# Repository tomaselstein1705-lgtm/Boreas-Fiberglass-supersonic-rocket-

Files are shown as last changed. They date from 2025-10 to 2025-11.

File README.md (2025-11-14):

# Boreas
Boreas is a full fiberglass 90cm long rocket, expected to reach up to 2km and fly over Mach 1 (Mach 1.2 actually), in an I205W high power motor, utilizing dual development and other high-power rocketry techniques. If you want to make it yourself, I recommend you first get your L1 with another rocket; handling fiberglass is very dangerous and difficult, so do it at your own risk!! Also, this rocket doesn't have any railguides, so you'll need to build a 40mm launch tower or just go to a club and use the one they have. Be really careful handling motors and always follow NAR/TRIPOLI rules!!!

# Boreas render
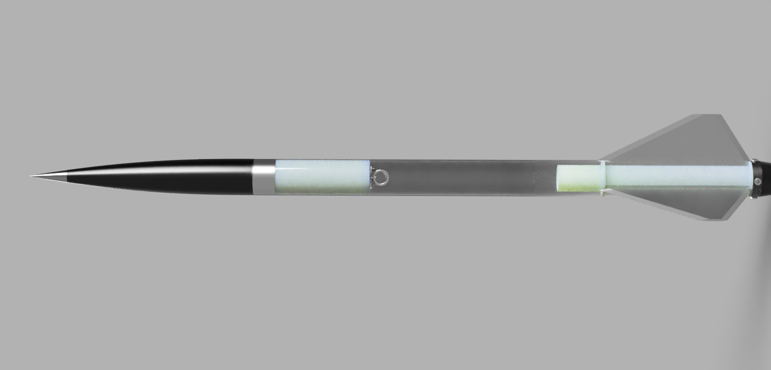
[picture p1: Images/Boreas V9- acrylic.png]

Full body (low visibility)

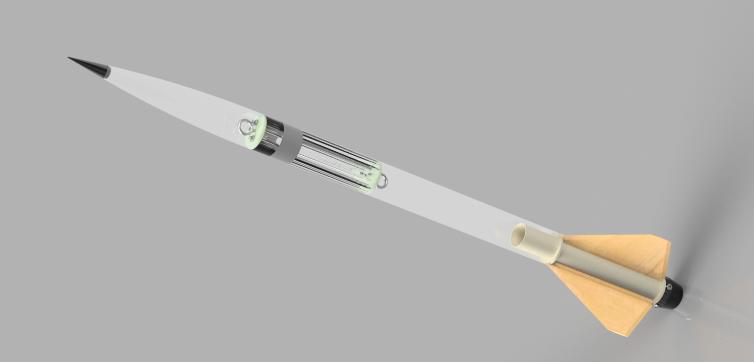
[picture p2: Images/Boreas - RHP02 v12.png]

Full body (Invisible body)

# BOM
(Without a motor, you can use an "I-205" or smaller, make simulations before flying)

| Name | Description | Quantity | Final Price | Link |
|---|---|---|---|---|
| Shock Cord - 1500 lb | Good quality, they are made for high power, and kevlar is the material of choice for shock cords | 4 m | $6.5 | https://www.mach1rocketry.com/product-page/kevlar-shock-cords |
| Centering rings | Made out of G10, they are precise and get the job done | 2 | $8 | https://www.mach1rocketry.com/product-page/g10-fiberglass-centering-rings |
| 29mm MMT | Good fiberglass mount | 9 in | $11.25 | https://www.mach1rocketry.com/product-page/fiberglass-motor-mount-tubes |
| Light fiberglass sleeve | Used to fabricate the nosecone; remnants are cheaper and work just as well | 15 ft | $7.95 | https://sollercompositesllc.com/product/remnants/ |
| 40mm Airframe | Premade, light, and inexpensive fiberglass airframe tube | 3 ft | $39 | https://www.mach1rocketry.com/product-page/fiberglass-airframe-tubes |
| Shock Cord - 1500 lb | Same kevlar shock cord as above | 4 m | $6.5 | https://www.mach1rocketry.com/product-page/fiberglass-coupler-tubes |
| 38mm avbay tube | The avionics fit inside this tube | 5 in | $8.75 | https://www.mach1rocketry.com/product-page/fiberglass-coupler-tubes |
| .9 grams charge wells | Holds the ejection charge; lightweight with a 3M screw on the bottom | 2 | $8 | https://www.mach1rocketry.com/product-page/charge-wells |
| Eggtimer Quark (backup) | Backup commercial flight computer for safety | 1 | $25 | https://eggtimerrocketry.com/purchase/ |
| HighTel (main flight computer) | Custom flight computer | 1 | None | https://github.com/tomaselstein1705-lgtm/HighTel |
| Terminal blocks | Connection point for pyro igniters; computers send charge through these | 1 | $2.5 | https://www.mach1rocketry.com/product-page/terminal-blocks |
| M4 Eye nuts | Cheap eye nuts including bolts and washers | 3 | $6 | https://www.mach1rocketry.com/product-page/eye-nuts |
| Thin mill drogue chute (9\") | Drogue locks in terminal velocity until main deployment; very durable brand | 1 | $6 | https://www.mach1rocketry.com/product-page/top-flight-thin-mill-parachutes |
| Thin mill parachute (24\") | Main chute brings descent to 6 m/s; durable and reliable | 1 | $19 | https://www.mach1rocketry.com/product-page/top-flight-thin-mill-parachutes |
| Table top epoxy (2 quart) | Used for tip-to-tip reinforcement and nosecone fabrication; cheap and effective | 1 | $34 | https://www.totalboat.com/products/table-top-epoxy-crystal-clear-resin |
| Aeropoxy ES6209 | Thick, strong, and affordable epoxy for fiberglass | 1 | $40 | https://giantleaprocketry.com/products/aeropoxy-structural-adhesive-kit |
| 3K Carbon Twill Weave | Carbon fiber cloth upgrade, sold by the yard | 1 yd | $19.99 | https://sollercompositesllc.com/product/3k-carbon-twill-weave-sold-by-the-running-yard-roll/ |

| **Total Cost:**                          |                                                                                                                                                                                        |          | **241.94$** |      |

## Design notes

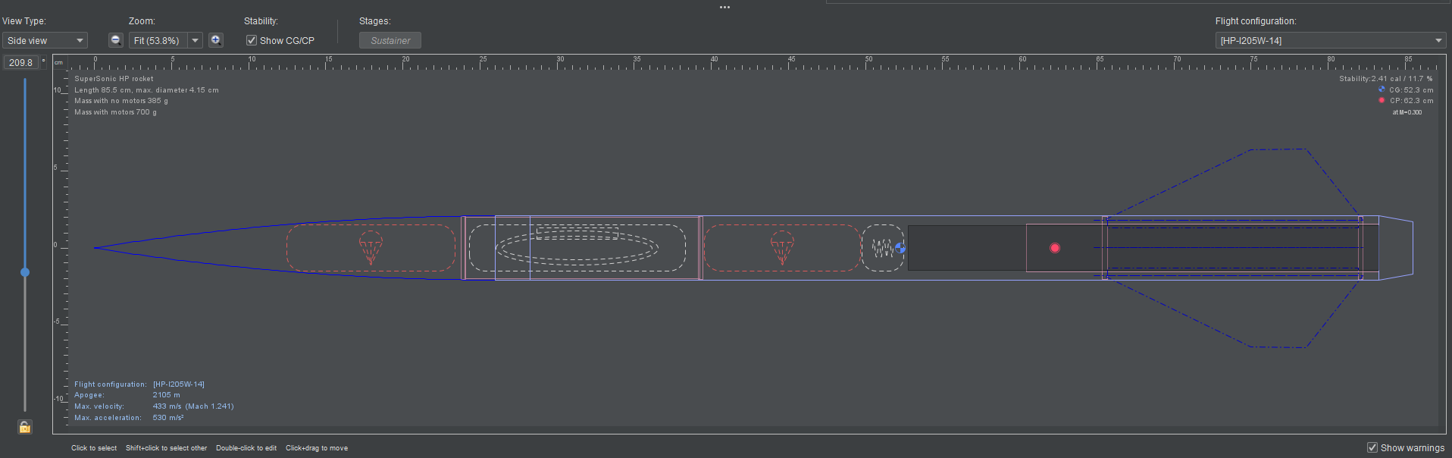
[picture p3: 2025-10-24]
Images/OrOverview.png

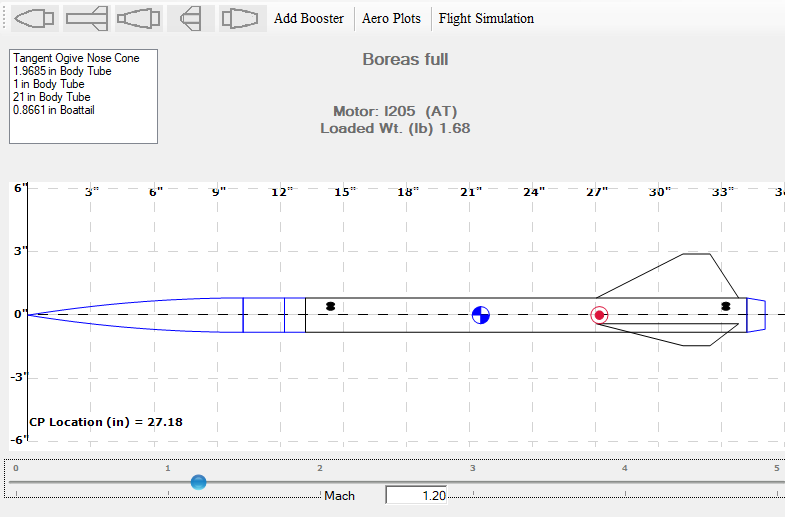
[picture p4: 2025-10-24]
Images/RASAoverview.png

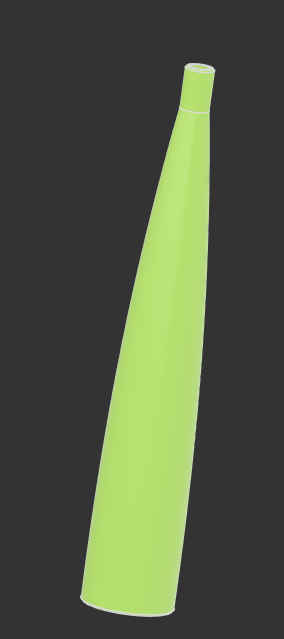
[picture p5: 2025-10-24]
Images/Noseconemodl.png

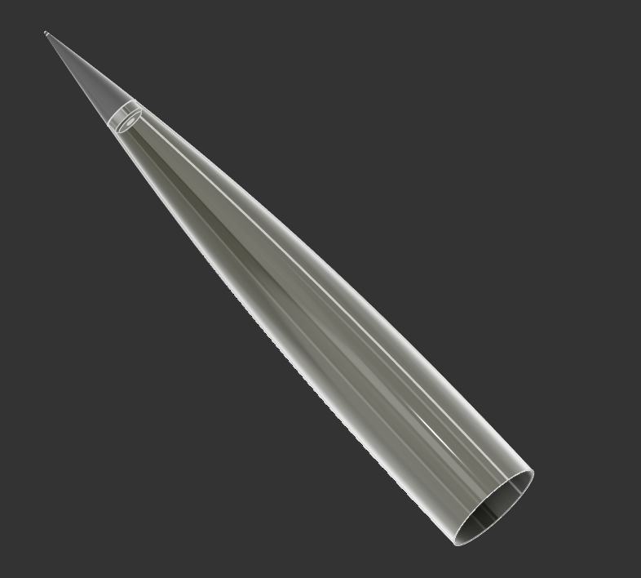
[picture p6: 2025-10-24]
Images/NoseCone.png

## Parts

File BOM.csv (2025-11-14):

Name | Description | Quantity | Final Price | Link
Shock Cord - 1500 lb | Good quality Kevlar cords for high power rockets | 4 m | $6.50 | https://www.mach1rocketry.com/product-page/kevlar-shock-cords
Centering Rings | Made of G10 fiberglass; precise and durable | 2 | $8.00 | https://www.mach1rocketry.com/product-page/g10-fiberglass-centering-rings
29mm MMT | Fiberglass motor mount tube | 9 in | $11.25 | https://www.mach1rocketry.com/product-page/fiberglass-motor-mount-tubes
I205 14A 29mm Motor | High-performance motor — the heart of the rocket | 1 | $64.00 | https://aerotech-rocketry.com/products/product_6195f3f3-6684-3bea-d54d-0b09b58c0427
Light Fiberglass Sleeve | Used for fabricating the nosecone; remnants are cost-effective | 15 ft | $7.95 | https://sollercompositesllc.com/product/remnants/
40mm Airframe | Premade fiberglass tube for rocket airframe — lightweight and affordable | 3 ft | $39.00 | https://www.mach1rocketry.com/product-page/fiberglass-airframe-tubes
38mm AvBay Tube | Houses avionics section of the rocket | 5 in | $8.75 | https://www.mach1rocketry.com/product-page/fiberglass-coupler-tubes
0.9g Charge Wells | Holds ejection charges; light and includes screw base | 2 | $8.00 | https://www.mach1rocketry.com/product-page/charge-wells
Eggtimer Quark (Backup) | Backup commercial flight computer for redundancy and safety | 1 | $25.00 | https://eggtimerrocketry.com/purchase/
HighTel (Main Flight Computer) | Custom flight computer — see GitHub repository | 1 | N/A | https://github.com/tomaselstein1705-lgtm/HighTel
Terminal Blocks | Connect pyro igniters; computer outputs current to these | 1 | $2.50 | https://www.mach1rocketry.com/product-page/terminal-blocks
M4 Eye Nuts | Includes bolts and washers; strong and affordable | 3 | $6.00 | https://www.mach1rocketry.com/product-page/eye-nuts
Thin Mill Drogue Chute (9”) | Drogue chute slows rocket to terminal velocity before main deploy | 1 | $6.00 | https://www.mach1rocketry.com/product-page/top-flight-thin-mill-parachutes
Thin Mill Parachute (24”) | Main parachute; reduces landing speed to ~6 m/s | 1 | $19.00 | https://www.mach1rocketry.com/product-page/top-flight-thin-mill-parachutes
Table Top Epoxy (2 Quart) | Used for tip-to-tip reinforcement and nosecone layup | 1 | $34.00 | https://www.totalboat.com/products/table-top-epoxy-crystal-clear-resin
Aeropoxy ES6209 | Strong structural epoxy for fiberglass bonding | 1 | $40.00 | https://giantleaprocketry.com/products/aeropoxy-structural-adhesive-kit-2-gallon
3k Carbon fiber Cloth | Way sturdier than fiberglass; ideal for composite layups | 1yd | $20.00 | https://sollercompositesllc.com/product/3k-carbon-twill-weave-sold-by-the-running-yard-roll/
 |  |  | Total: | 287.95$

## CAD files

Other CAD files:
Boreas Fusion360.f3z

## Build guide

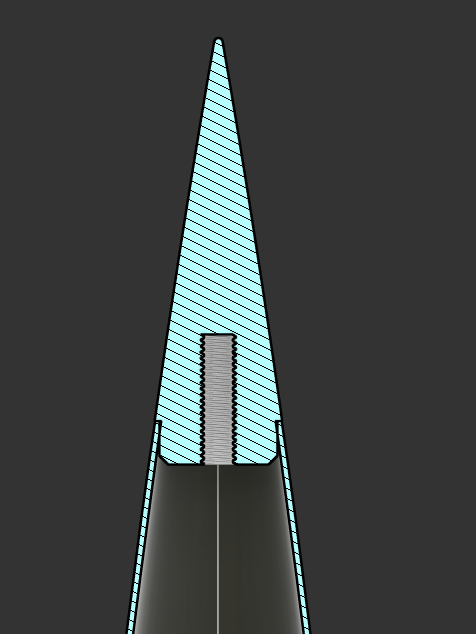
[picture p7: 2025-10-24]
Images/TipAssembly.png

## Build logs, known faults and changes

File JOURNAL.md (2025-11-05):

<!--
  ===================    !!READ THIS NOTICE!!   ====================
  DO NOT edit this file manually. Your changes WILL BE OVERWRITTEN!
  This journal is auto generated and updated by Hack Club Blueprint.
  To edit this file, please edit your journal entries on Blueprint.
  ==================================================================
-->

## 10/24/2025 - High power composite rocket  

## 10/24/2025 - High power composite rocket  

# Design overview
Hi, this is my project; it's going to be my first supersonic rocket. I designed it all around fiberglass and plywood. I divided the design of this project into **4 sections**: 1. Research, 2. Aerodynamics and Stability. 3- Motor mount - fin can design. 4- Avbay designing - avionics 5- Nosecone - Recovery. 
My objective is to use fiberglass for the first time and be one of the first in my country (Paraguay) to break the speed of sound, plus gain some more experience in high-power rocketry.

# **1- Research**
I first researched the changes while going supersonic. Once you go supersonic, the CP of the rocket **starts moving forward**. I need a high-caliper rocket. My rocket is going to fly a few km up, so I need something to get the recovery as low as possible. Fortunately, there's something called dual development that can get your rocket´s retrieval distance down significantly!! For the speed and forces I'm pushing my rocket, I should use something rigid, because the pressure that gets when going supersonic is really high, and an I-205W has a max impulse of 253 newtons; cardboard isn't an option anymore, so I chose fiberglass. Making the fins out of fiberglass was going to be reallyyy expensive, so I chose to make them out of plywood and then make a tip-to-tip with some more fiberglass, which would add a lot of rigidity to the final model.
(5 hours)

# **2- Aerodynamic stability**

- OpenRocket design (sub-sonic)

- RASAero design (supersonic)
-Firstly, in OpenRocket, I designed the structure of the airframe, where I assigned the materials, motor, airframe size, and fin size. I added a boat tail to reduce drag, dual development (The nosecone has the main parachute, which gets opened 150 m above ground level by a flight computer, and the booster section has the drogue; the drogue gets deployed during apogee), and I included "through-the-wall" fins to distribute the thrust of the motor around the whole airframe.
Then, in RASAero, I checked the stability at supersonic speeds and some other drag stuff.
(2 hours)

# **3- Motor mount - fin can designing**

This is the design of my fin can-motor mount. I'll use a fiberglass motor mount tube, centering rings, and an airframe. Still, as said before, I'm using plywood for my fins, with 3 holes that get into the airframe to distribute loads. Then I'll laminate 2 layers of 6oz fiberglass over it, finding a good, cheap-quality epoxy for "laminating" fiberglass (what im doing with the nosecone and fins) was very hard. Firstly, I wanted to buy some epoxy from West Systems, but a few liters of that epoxy were like 100$!! So I did some more research and I found the total boat, they have some good epoxy, but it was still very expensive, but then I found out that I could use table top epoxy for the job, and this one was just 40$!! So I went with this one, same for the adhesive, I wanted to use JB weld, but I found "Aeropoxy Structural Adhesive", which is just 40$for  the 2 liters, so I also went for this as my adhesive

The boat tail is going to be made out of PETG-CF, and it's going to get screwed in with 4, 4M screws. It also works as a motor reteiner; this part is essential to hold the motor during the parachute ejection.
(2.2 hours)

# **4- Avbay design - avionics**


My avbay is an inside tube that holds both of my flight computers, it has 2, 0.9 grams pyros on the top, one is going to be connected to my; it connects the nosecone with the booster section. It also holds my avionics, my main is High Tel (still in progress), and my secondary is an Eggtimer Quark (Commercial for safety). This will all work with a 1, 7V Lipo and a 1, 3,3v Lipo. Now, in the structure, the main tube is a 38-36mm fiberglass tube. I have 2 fiberglass bulkheads to protect the top and bottom of the avbay; this also holds 2 eye-bolts, which get tied into the shock cord. The ring that is in the middle is called "switch band", this piece is in charge of stopping the avbay from sliding further into the airframe-nosecone. I have 2 M4 threaded rods, which are in charge of pressing everything together and holding my avionics in place.
(1.2 hours)

# **5- Nosecone - Recovery**


This is my nosecone; it's made out of fiberglass. For making this nosecone, I'm going to use this mold:


It has the size of the inside of the nosecone. I'm going to lay up fiberglass sleeves to make the outside of the nosecone, like the picture above, then I'm gonna hammer it out:



As I can't make the tip from fiberglass because of the size, I'm going to make it out of aluminum with JLC. This gets secured with an eye bolt, which also provides an M4 attachment point for the shock cord.


For recovery, I'm going to use 2 "parachutes", a drogue (9" thin mill parachute) in the booster section (This one gets deployed at apogee), and as a main parachute, a top-flight 24" thin mill parachute, this one is located on the nosecone, it gets deployed 100m agl, for the shock cord im using kelvar, as this has some steel like strength, for my case, the best option is the 1500lb one (kinda over-kill, but i want more than less).
(2 hours)

# BOM

| Name: | Description: | Quantity: | Final Price: | Link: |
| --- | --- | --- | --- | ----- |
| Shock Cord - 1500 lb | Good quality, they are made for high power, and kevlar is the material of choise for shock cords  | 4 m | $6.5 | [Mach 1 Rocketry](https://www.mach1rocketry.com/product-page/kevlar-shock-cords)  |
| Centering rings | Made out of G10, they are precise and get the job done | 2 | $8 | [Mach 1 Rocketry](https://www.mach1rocketry.com/product-page/g10-fiberglass-centering-rings) |
| 29mm MMT | Good fiberglass mount | 9 in | 11.25$ | [Mach 1 Rocketry](https://www.mach1rocketry.com/product-page/fiberglass-motor-mount-tubes)  |
| 3M 2 filter respirator | This is a must for fiberglass, beacuse fiberglass dust is good for rockets but not for your lungs, so you need to use a respirator or you can do some really bad damage to your lungs, this is the best quality-price i could find | 100 | 45$ | [Amazon](https://www.amazon.com/3M-7513PA1-Professional-Organic-Respirator/dp/B0009JNF1I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)  |
| I205 14A 29mm motor | This is the heart of the project, the motor | 1 | 64 | [Aerotech](https://aerotech-rocketry.com/products/product_6195f3f3-6684-3bea-d54d-0b09b58c0427) |
| Light fiberglass sleeve | These are used to fabricate the nosecone, the remants are way cheaper and you get basically the same product | 15 ft | 7.95$ | [Soller composites](https://sollercompositesllc.com/product/remnants/)  |
| 40mm Airframe  | The airframe of the rocket, its premade and light, very cheap | 3 ft | 39$ | [Mach 1 Rocketry](https://www.mach1rocketry.com/product-page/fiberglass-airframe-tubes)  |
| Shock Cord - 1500 lb | Good quality, they are made for high power, and kevlar is the material of choise for shock cords  | 4 m | $6.5 | [Mach 1 Rocketry](https://www.mach1rocketry.com/product-page/fiberglass-coupler-tubes)  |
| 38mm avbay tube | The avionics fit inside of here | 5 in | $8.75 | [Mach 1 Rocketry](https://www.mach1rocketry.com/product-page/fiberglass-coupler-tubes) |
| .9 grams charge wells | The ejection charge for the second half of the rocket fits in here, this is a light and cheap one, it has a 3M scew in the bottom | 2 | 8$ | [Mach 1 Rocketry](https://www.mach1rocketry.com/product-page/charge-wells)  |
| Egg timer quark (backup) | This is the backup flight computer, I need to use a commercial for safety | 1 | 25$ | [Eggtimer](https://eggtimerrocketry.com/purchase/)  |
| HighTel (main flight computer) | This is my flight computer [Github repository](https://github.com/tomaselstein1705-lgtm/HighTel) | 1 | None | [Project](https://github.com/tomaselstein1705-lgtm/HighTel) |
| Terminal blocks | You connect the pyro´s igniters to here and the computers gives charge to the terminal blocks | 1 | 2.5$ | [Mach 1 rocketry](https://www.mach1rocketry.com/product-page/terminal-blocks)  |
| M4 Eye nuts  | They are kinda cheap, and they include the bolts and washers. | 3 | 6$ | [Mach 1 Rocketry](https://www.mach1rocketry.com/product-page/eye-nuts)  |
| Thin mill drouge chute (9") | The drouge gets the speed of the rocket locked in its terminal veloticity until main deploy, and Top Flight is a very durable and good brand | 1 | 6$ | [Mach 1 rocketry](https://www.mach1rocketry.com/product-page/top-flight-thin-mill-parachutes)  |
| Thin mill parachute (24") | The Parachute gets the speed of the rocket to 6m/s, a safe touch down velocity and Top Flight is a very durable and good brand | 1 | 19$ | [Mach 1 rocketry](https://www.mach1rocketry.com/product-page/top-flight-thin-mill-parachutes) |
| Table top epoxy (2 quart) | Used for the Tip-to-tip and to  make the nosecone, its the chapest and best one for the use | 1 | 34$ | [Total Boat](https://www.totalboat.com/products/table-top-epoxy-crystal-clear-resin?variant=43150894661856)  |
| Aeropoxy ES6209 | Perfect for fiberglass, very thick and cheap | 1 | 40$ | [Aeropoxy](https://giantleaprocketry.com/products/aeropoxy-structural-adhesive-kit-2-gallon?variant=37741182386348)  |
| 6oz fiberglass  | Perfect fiberglass, very cheap | 1 | 18$ | [Amazon](amazon.com/Fiberglass-Glass-Inches-Fabric-Surfboard/dp/B0B3SXHSDP/ref=sr_1_3?crid=3CWRS3MYVO21J&dib=eyJ2IjoiMSJ9.ONpdJw9UiIj-VZJu-D7rr454KJSNKobp1XPB_Zy4NApVdbfGpnPeOG_T8Utjymni2p65k5pNag8lwJjhTDtEJRpm3KMwnrCd50bhGeIeMJ2H1F5iiUuwlq-n2nNbf0G3s4cbA242VpkoaJD9sXSE7qxfmb2oFjLnF60ODP-7e-wktdT-cvecUEhx3YKpF-4YSICspa1oWRtxTH_5XDqbSn8mXhcZIXMAP6fr7yvCr1Q.0iZrHeBzOhw6GmNZpoqLNdNQ0W0ijjzPs2c2ZS556GM&dib_tag=se&keywords=6+oz+fiberglass&qid=1761339206&sprefix=6+oz+fiberglass%2Caps%2C467&sr=8-3)  |
| Total Cost: | | | 348.95$ | |

## 11/5/2025 - Fixed BOM  

Screenshot_20251105_164338_Chrome
I used the worng format in the BOM so it looked messed up, I corrected it and make it look prettier and more appeling to people interested in the cost of the project.

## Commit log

2025-10-21 Boreas - CAD. f3z
    [Boreas - RHP02 v14.f3z]
2025-10-23 Rename Boreas - RHP02 v14.f3z to Boreas Fusion360.f3z
    [Boreas Fusion360.f3z]
2025-10-24 Update Boreas BOM .csv
    [Boreas BOM .csv]
2025-10-24 Update and rename Boreas BOM .csv to Boreas BOM
    [Boreas BOM .csv]
2025-10-24 Update Boreas BOM
2025-10-24 Update and rename Boreas BOM to BOM.csv
    [BOM.csv]
